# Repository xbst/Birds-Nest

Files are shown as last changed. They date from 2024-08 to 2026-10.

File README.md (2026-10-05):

# Birds' Nest Toolchanger USB Hub
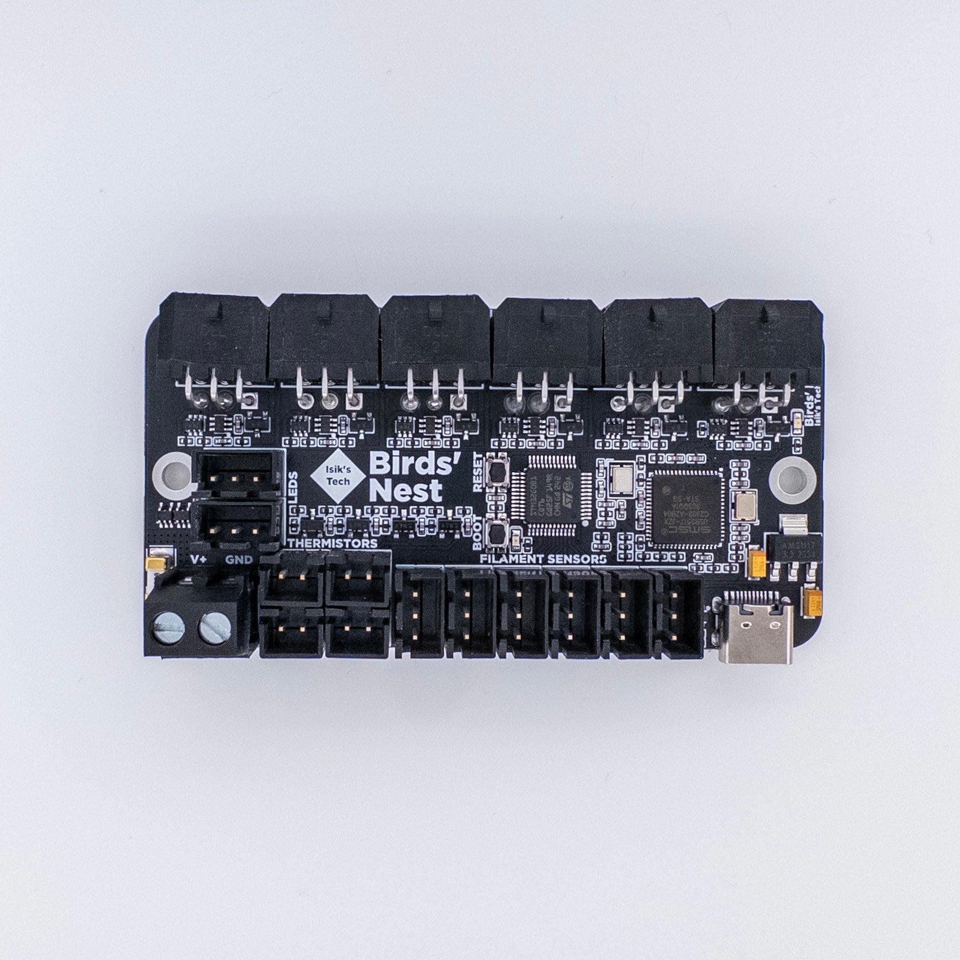
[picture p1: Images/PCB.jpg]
Birds' Nest PCB


Birds' Nest is a USB hub PCB designed for toolchanger printers with USB toolhead PCBs. It features:
- 6x USB Outs for Up To 6 Toolheads, Protected
- 6x Filament Sensor Connectors
- 4x Thermistor Connectors
- 2x 5V RGB Connectors

## Purchasing a Birds' Nest

[Isik's Tech Official Store](https://store.isiks.tech/products/birds-nest)

## Instructions

[Birds' Nest Manual](https://docs.isiks.tech/birds-nest/usb/manual/)

## YouTube

I am a YouTube content creator. If you want content about these projects & more, please consider [subscribing to my YouTube channel](https://www.youtube.com/channel/UClAWYmCkHjsbaX9Wz1df2mg).

## Notes
- Markdown files in this repository may contain Amazon Associate, Aliexpress affiliate, PCBWay affiliate, Jawstec affiliate, Polymaker affiliate links. I make a comission on qualifying purchases.
- This project does not come with any warranty, if you choose to build/use a PCB manufactured using published files in this repository, you are doing this at your own risk!
- If you want to sell PCBs manufactured using published files in this repository, you are allowed to, and you will not owe me any royalties. **You cannot claim that I endorse the sale**. You can check the license file for more information. However, if you **wish** to give me a share you can sponsor me on [GitHub](https://github.com/sponsors/xbst), subscribe on [Patreon](https://l.isiks.tech/patreon) or [YouTube](https://l.isiks.tech/member).

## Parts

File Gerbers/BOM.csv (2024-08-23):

ID | Name | Designator | Footprint | Quantity | Manufacturer Part | Manufacturer | Supplier | Supplier Part | Price
1 | 1uF | C14,C12,C13,C18,C23 | C0402 | 5 | CL05A105KA5NQNC | SAMSUNG(三星) | LCSC | C52923 | 0.003
2 | 12kΩ | R55,R15,R30 | R0402 | 3 |  | UNI-ROYAL(厚声) | LCSC | C25752 | 0.001
3 | 24MHz | X1 | OSC-SMD_4P-L3.2-W2.5-BL | 1 | S3D24.000000B20F30T | SCTF(星通时频) | LCSC | C387391 | 0.413
4 | 36kΩ | R45,R46,R47,R48,R49,R50,R51,R52,R53,R54,R13,R14,R16,R17,R27 | R0402 | 15 |  | UNI-ROYAL(厚声) | LCSC | C43676 | 0.001
5 | 470Ω | R43,R44 | R0402 | 2 | 0402WGF4700TCE | UNI-ROYAL(厚声) | LCSC | C25117 | 0.001
6 | B3B-XH-A-BK(LF)(SN) | RGB1,RGB2,FS1,FS2,FS3,FS4,FS5,FS6 | CONN-TH_3P-P2.50_B3B-XH-A-BK-LF-SN | 8 | B3B-XH-A-BK(LF)(SN) | JST | LCSC | C493416 | 0.085
7 | SN74AHCT1G125DCKR | U4,U5 | SC-70-5_L2.0-W1.3-P0.65-LS2.1-BL | 2 | SN74AHCT1G125DCKR | TI(德州仪器) | LCSC | C350557 | 0.08
8 | EVPAA202K | BOOT,RESET | KEY-SMD_4P-L3.5-W2.9-P1.48-LS4.3-TL | 2 | EVPAA202K | PANASONIC(松下) | LCSC | C79147 | 0.354
9 | 100nF | C1,C2,C3,C4,C5,C6,C7,C8,C9,C10,C11,C19,C20,C21,C22,C24,C25,C26,C27,C28,C29,C32,C33,C34,C35 | C0402 | 25 | CL05B104KB54PNC | SAMSUNG(三星) | LCSC | C307331 | 0.005
10 | 30pF | C30,C31 | C0402 | 2 | 0402CG300J500NT | FH(风华) | LCSC | C1570 | 0.001
11 | 10u | C16,C17 | CAP-SMD_L3.2-W1.6-R-RD | 2 | TAJA106K016RNJ | AVX | LCSC | C7171 | 0.093
12 | BAV70 | D1,D4,D6,D7,D10,D12 | SOT-23-3_L3.0-W1.7-P0.95-LS2.9-BR | 6 | BAV70 | CJ(江苏长电/长晶) | LCSC | C68978 | 0.019
13 | TPNUP2301MW6T1G | D2,D3,D5,D8,D9,D11,D13 | SOT-363_L2.0-W1.3-P0.65-LS2.1-BL | 7 | TPNUP2301MW6T1G | TECH PUBLIC(台舟) | LCSC | C708740 | 0.117
14 | BAV99,215 | D14,D15,D16,D17 | SOT-23-3_L2.9-W1.6-P1.90-LS2.8-BR | 4 | BAV99,215 | Nexperia(安世) | LCSC | C2500 | 0.008
15 | 0451020.MRL | F1 | FUSE-SMD_L6.1-W2.7 | 1 | 0451020.MRL | Littelfuse(美国力特) | LCSC | C178980 | 0.909
16 | LED-0603_B | MCU,VCC | LED0603_BLUE | 2 | 19-217/BHC-ZL1M2RY/3T | EVERLIGHT(台湾亿光) | LCSC | C72041 | 0.021
17 | HC-MX3.0-2*3AW | OUT1,OUT2,OUT3,OUT4,OUT5,OUT6 | CONN-TH_6P-P3.00_HC-MX3.0-2X3AW | 6 | HC-MX3.0-2*3AW | HCTL(华灿天禄) | LCSC | C3294384 | 0.215
18 | NTJD4001NT1G | Q1,Q2,Q3,Q4,Q5,Q6 | SOT-363_L2.0-W1.3-P0.65-LS2.1-TL | 6 | NTJD4001NT1G | onsemi(安森美) | LCSC | C190019 | 0.099
19 | 100kΩ | R1,R6,R9,R10,R18,R24 | R0402 | 6 | 0402WGF1003TCE | UNI-ROYAL(厚声) | LCSC | C25741 | 0.001
20 | 100Ω | R2,R3,R4,R5,R7,R8,R11,R12,R19,R23,R25,R26 | R0402 | 12 | 0402WGF1000TCE | UNI-ROYAL(厚声) | LCSC | C25076 | 0.001
21 | 5.1kΩ | R21,R22 | R0402 | 2 | RC0402FR-075K1L | YAGEO(国巨) | LCSC | C105872 | 0.001
22 | 1.5kΩ | R20,R29 | R0402 | 2 | 0402WGF1501TCE | UNI-ROYAL(厚声) | LCSC | C25867 | 0.001
23 | 10Ω | R28 | R0402 | 1 | 0402WGF100JTCE | UNI-ROYAL(厚声) | LCSC | C25077 | 0.001
24 | 4.7kΩ | R31,R36,R37,R42 | R0402 | 4 | 0402WGF4701TCE | UNI-ROYAL(厚声) | LCSC | C25900 | 0.001
25 | 2.37K | R32,R33,R34,R35,R38,R39,R40,R41 | R0402 | 8 | RC0402FR-072K37L | YAGEO(国巨) | LCSC | C294439 | 0.001
26 | B2B-XH-A-BK(LF)(SN) | TH1,TH2,TH3,TH4 | CONN-TH_2P-P2.50_JST_B2B-XH-A-M | 4 | B2B-XH-A-BK(LF)(SN) | JST | LCSC | C378939 | 0.048
27 | USB2517-JZX | U1 | QFN-64_L9.0-W9.0-P0.50-BL-EP4.8 | 1 | USB2517-JZX | MICROCHIP(美国微芯) | LCSC | C1521556 | 6.026
28 | AMS1117-3.3 | U2 | SOT-223-3_L6.5-W3.4-P2.30-LS7.0-BR | 1 | AMS1117-3.3 | AMS | LCSC | C6186 | 0.136
29 | STM32G0B1CBT6 | U3 | LQFP-48_L7.0-W7.0-P0.50-LS9.0-BL | 1 | STM32G0B1CBT6 | ST(意法半导体) | LCSC | C2847904 | 1.874
30 | USB3.1C16PFSMT | USBC | USB-C-SMD_TYPE-C-USB-17 | 1 | - | LCSC | LCSC | C167321 | 0.356
31 | DB128L-5.08-2P-BK-S | VIN | CONN-TH_2P-P5.08_DB128L-5.08-2P-BK-S | 1 | DB128L-5.08-2P-BK-S | DORABO(地博电气) | LCSC | C430601 | 0.182
32 | 8MHz | X2 | CRYSTAL-SMD_4P-L3.2-W2.5-BL-2 | 1 | 3TJ480000ZYLBC | JYJE(晶友嘉) | LCSC | C2924619 | 0.198
33 | NO | 3.3V,GND,NRST,SWCLK,SWDIO,USB_RST,USB_SCL,USB_SDA | TP | 8

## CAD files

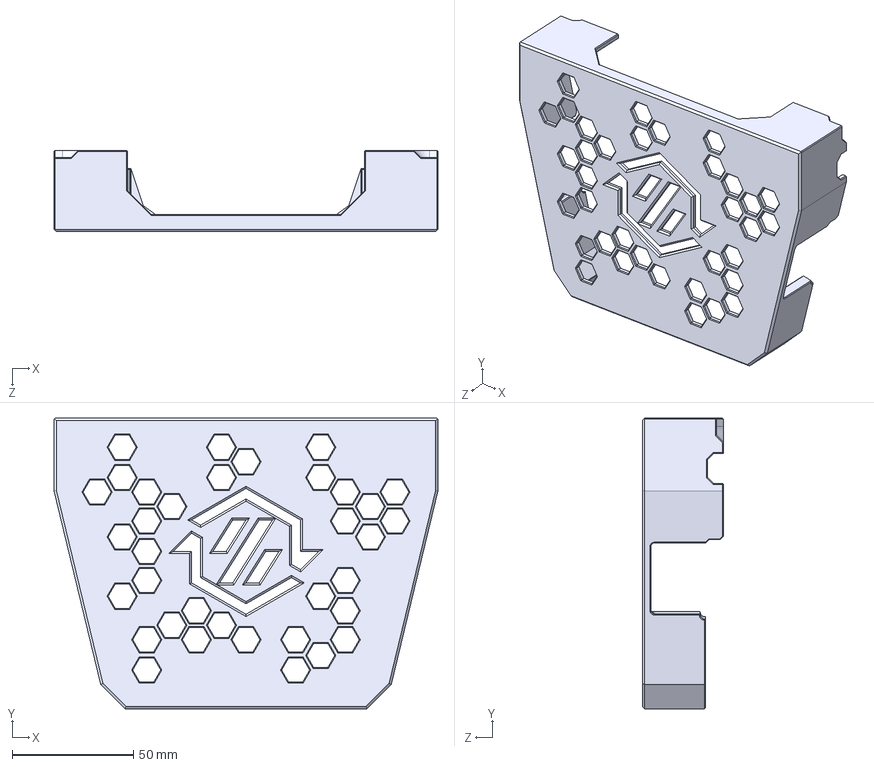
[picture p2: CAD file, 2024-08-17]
CAD/Mounts/V2/Fannypack_Cover.STEP
158.6 x 120.0 x 33.6 mm

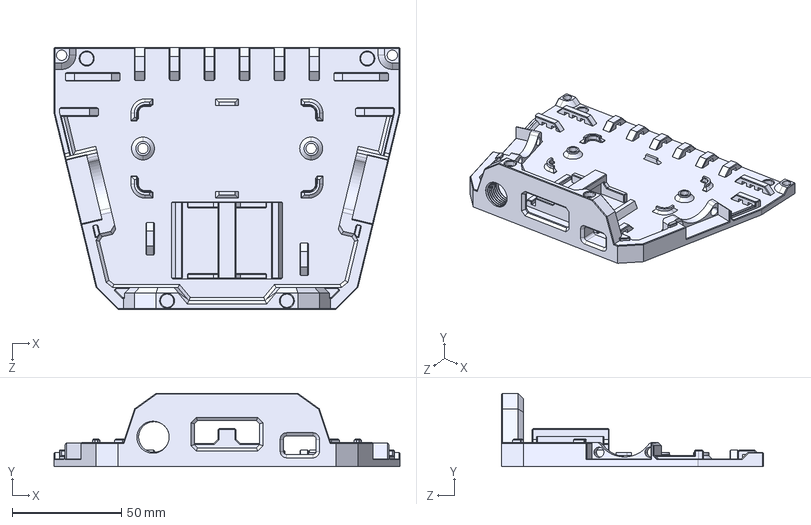
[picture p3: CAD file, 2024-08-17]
CAD/Mounts/V2/Fannypack_Base.STEP
158.6 x 33.6 x 120.0 mm

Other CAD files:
Mounts/V2/Fannypack_Base.STL
Mounts/V2/Fannypack_Cover.STL

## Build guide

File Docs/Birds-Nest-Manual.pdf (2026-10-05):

## Birds' Nest (USB) Manual

Birds ' Nest documentation | mo ved to a new documenta | tion site :
https://docs.isiks.tech/birds | -nest/usb/manual/ (https://docs.isiks.tech/birds-nest/usb/manual/)

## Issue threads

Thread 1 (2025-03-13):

D1, D4, D6, D7, D10, D12 too weak?

dgo42, 2025-03-13:
Hello, you use dual BAV70 diode to provide 24V power single Toolhead PCB.
Some hotends consumes 40W, some 60W, some even 70W. First 10-20s hotend will be powered 100%.
This means we need alone for hotend 2.9A current.
In addition toolhead PCB has extruder motor driver which can consume up to 0.2A.
Single BAV70 can pass up to 0.25A, dual up to 0.5A
IMO this diode are to weak, in addition forward voltage @ 0,25A is 1.25V. It means, that toolhead gets only 22.75V instead of 24V.
I suggest to change BAV70 to some schottky and some more powerful

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

xbst, 2025-03-13:
Toolhead current isn't flowing through that diode

dgo42, 2025-03-13:
Oh, I looked in wrong direction 🤦🏻‍♂️ It's D13 ESD suppression and not a connector 🤣. Sorry

Closed 2025-03-13.

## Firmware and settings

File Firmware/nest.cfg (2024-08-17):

[mcu nest]
serial: /dev/serial/by-id/usb-Klipper_stm32g0b1xx_300030000850304158373420-if00
# Edit with the serial of Birds' Nest. Use ls /dev/serial/by-id/* to find it.

[filament_switch_sensor FS1]
switch_pin: ^nest:PB9

[filament_switch_sensor FS2]
switch_pin: ^nest:PB8

[filament_switch_sensor FS3]
switch_pin: ^nest:PB7

[filament_switch_sensor FS4]
switch_pin: ^nest:PB6

[filament_switch_sensor FS5]
switch_pin: ^nest:PB5

[filament_switch_sensor FS6]
switch_pin: ^nest:PB4

[temperature_sensor TH1]
sensor_type: Generic 3950
sensor_pin: nest:PA2
pullup_resistor: 4700

[temperature_sensor TH2]
sensor_type: Generic 3950
sensor_pin: nest:PA3
pullup_resistor: 4700

[temperature_sensor TH3]
sensor_type: Generic 3950
sensor_pin: nest:PA6
pullup_resistor: 4700

[temperature_sensor TH4]
sensor_type: Generic 3950
sensor_pin: nest:PA7
pullup_resistor: 4700

[temperature_sensor Birds_Nest_Temp]
sensor_type: temperature_mcu
sensor_mcu: nest
min_temp: 0
max_temp: 100

[neopixel NEO1]
pin: nest:PD3
color_order: GRBW

[neopixel NEO2]
pin: nest:PB3
color_order: GRBW
